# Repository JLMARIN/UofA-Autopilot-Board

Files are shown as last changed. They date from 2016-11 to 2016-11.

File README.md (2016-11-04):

# UofA-Autopilot-Board
University of Alberta Autopilot Board Hardware Design

This repository holds the design files for the University of Alberta Autopilot Board, currently being used by the University of Alberta Aerial Robotics Group (UAARG).

This project was developed by Jorge Marin, Rijesh Augustine and Duncan G. Elliott, from the University of Alberta ECE department.

The current design files include both the autopilot board and the redundant power supply board inside a single file. both board are connected by a breakaway tab. The reason for keeping both boards together is for reducing manufacturing costs. They can be separted afterwards.

A user guide is also included that contains comprehensive information about the autopilot board. A similar guide for the redundant power supply board is under work right now and will be available once finished.

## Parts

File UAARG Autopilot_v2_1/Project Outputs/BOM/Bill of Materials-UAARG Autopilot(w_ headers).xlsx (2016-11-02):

Designator | Description | Quantity | Value | Manufacturer | Manufacturer Part Number | Supplier 1 | Supplier Part Number 1
C1, C2 | Capacitor | 2 | 10pF | Yageo | CC0402JRNPO9BN100 | Digi-Key | 311-1014-1-ND
C3, C4, C5, C23, C36, C49, C67, C80 | Capacitor | 8 | 2.2uF | Yageo | CC0402MRX5R5BB225 | Digi-Key | 311-1442-1-ND
C6, C24 | Capacitor | 2 | 4.7uF | Yageo | CC0603KRX5R6BB475 | Digi-Key | 311-1455-1-ND
C7, C8, C9, C10, C12, C13, C15, C16, C19, C20, C22, C35, C48, C52, C53, C54, C55, C56, C66, C79, C83 |  | 21 | 100nF | Yageo | CC0402KRX7R6BB104 | Digi-Key | 311-1345-1-ND
C11 | Capacitor | 1 | 1uF | Yageo | CC0402KRX5R5BB105 | Digi-Key | 311-1438-1-ND
C14 | Capacitor | 1 | 2.2nF | Yageo | CC0402KRX7R9BB222 | Digi-Key | 311-1037-1-ND
C17, C38, C51, C69, C82 | Capacitor | 5 | 4.7uF | Yageo | CC0402MRX5R6BB475 | Digi-Key | 311-1734-1-ND
C18 | Capacitor | 1 | 220nF | Yageo | CC0402KRX5R5BB224 | Digi-Key | 311-1681-1-ND
C21 | Polarized Capacitor | 1 | 33uF | Kemet | T491A336K010AT | Digi-Key | 399-5279-1-ND
C25, C37, C50, C68, C81 | Capacitor | 5 | 10nF | Yageo | CC0402KRX7R7BB103 | Digi-Key | 311-1042-1-ND
C27, C40, C58, C71 | CAP CER 0.1UF 10V 10% X7R 0402 | 4 | 0.47uF | Yageo | CC0402ZRY5V7BB474 | Digi-Key | 311-1735-1-ND
C28, C41, C59, C72 | Capacitor | 4 | 10uF | Samsung Electro-Mechanics America, Inc. | CL32B106KBJNNNE | Digi-Key | 1276-3387-1-ND
C29, C42, C60, C73 | Capacitor | 4 | 4.7uF | Samsung Electro-Mechanics America, Inc. | CL32B475KBUYNNE | Digi-Key | 1276-1292-1-ND
C30, C43, C61, C74 | CAP CER 0.1UF 10V 10% X7R 0402 | 4 | 100pF | Yageo | CC0402JRNPO9BN101 | Digi-Key | 311-1024-1-ND
C31, C32, C44, C45, C62, C63, C75, C76 | Capacitor | 8 | 47uF | Murata Electronics North America | GRM32ER71A476KE15L | Digi-Key | 490-5312-1-ND
C33, C46, C64, C77 | Capacitor | 4 | 10uF | Yageo | CC0805KKX5R7BB106 | Digi-Key | 311-1865-1-ND
C34, C47, C65, C78 | Capacitor | 4 | 100nF | Yageo | CC0603KPX7R7BB104 | Digi-Key | 311-1335-1-ND
C85, C86 | Capacitor | 2 | 8.2pF | Yageo | CC0402BRNPO9BN8R2 | Digi-Key | 311-1628-1-ND
C87 | Polarized Capacitor | 1 | 11mF | Seiko Instruments | CPH3225A | Digi-Key | 728-1067-1-ND
C88 | Capacitor | 1 | 33nF | Samsung Electro-Mechanics America, Inc. | CL05B333JO5NNNC | Digi-Key | 1276-1553-1-ND
C89 | Capacitor | 1 | 470pF | TDK Corporation | C1005C0G1H471J050BA | Digi-Key | 445-2656-1-ND
D1, D2 | Typical Schottky Diode | 2 |  | Toshiba Semiconductor and Storage | CMS04(TE12L,Q,M) | Digi-Key | CMS04(TE12LQM)CT-ND
D3 | Typical SchottkyDiode | 1 |  | Diodes Incorporated | 1N5819HW-7-F | Digi-Key | 1N5819HW-FDICT-ND
D4 | Typical Diode | 1 |  | Micro Commercial Co | 1N4148WX-TP | Digi-Key | 1N4148WXTPMSCT-ND
EX1, EX2 | Header, 10-Pin | 2 |  | Sullins Connector Solutions | NPPN101BFCN-RC | Digi-Key | S5751-10-ND
J6, J11, J12, J13, J14, J20 | Header, 4-Pin | 6 |  | Molex, LLC | 0533980471 | Digi-Key | WM7608CT-ND
J16 | Header, 6-Pin | 1 |  | 3M | 961106-5500-AR-PR | Digi-Key | 3M9501CT-ND
J17 | U.FL RF connector | 1 |  | Hirose Electric Co Ltd | U.FL-R-SMT(10) | Digi-Key | H9161CT-ND
J18 | SMA RF connector | 1 |  | Cinch Connectivity Solutions Johnson | 142-0701-801 | Digi-Key | J502-ND
J19 | Header, 7-Pin | 1 |  | Molex, LLC | 0533980771 | Digi-Key | WM7611CT-ND
J21 | Header, 5-Pin | 1 |  | Molex, LLC | 0533980571 | Digi-Key | WM7609CT-ND
JTAG1 | Mini JTAG connector header 10 pos 5x2 pitch 1.27mm TH | 1 |  | Samtec Inc. | FTSH-105-01-F-DV-K | Digi-Key | SAM8796-ND
L1 | BEAD FERRITE | 1 |  | Murata Electronics North America | BLM15AX102SN1D | Digi-Key | 490-5442-1-ND
L2, L3, L4, L5 | FIXED IND 6.8UH 7A 33.4 MOHM SMD | 4 | 6.8uH | Vishay Dale | IHLP3232DZER6R8M11 | Digi-Key | 541-1355-1-ND
L6 | Chip Inductor | 1 | 6.8nH | Murata Electronics North America | LQW15AN6N8H00D | Digi-Key | 490-6841-1-ND
L7 | Chip Inductor | 1 | 27nH | Murata Electronics North America | LQW15AN27NJ00D | Digi-Key | 490-1151-1-ND
LED1, LED5 | LED RED CLEAR 0603 SMD | 2 |  | Lite-On Inc. | LTST-C190KRKT | Digi-Key | 160-1436-1-ND
LED2 | LED ORANGE CLEAR 0603 SMD | 1 |  | Lite-On Inc. | LTST-C190AKT | Digi-Key | 160-1180-1-ND
LED3, LED6, LED8, LED9 | LED GREEN CLEAR 0603 SMD | 4 |  | Lite-On Inc. | LTST-C190KGKT | Digi-Key | 160-1435-1-ND
LED4, LED7 | LED YELLOW CLEAR 0603 SMD | 2 |  | Lite-On Inc. | LTST-C190YKT | Digi-Key | 160-1184-1-ND
Q1 | NPN General Purpose Amplifier | 1 |  | Diodes Incorporated | MMDT5551-7-F | Digi-Key | MMDT5551-FDICT-ND
Q2 | N-CH MOSFET W/ DIODE DUAL PACKAGE | 1 |  | NXP Semiconductors | BSS138PS,115 | Digi-Key | 568-8393-1-ND
R1, R5, R9, R17, R26, R33, R40, R41, R46, R49, R56, R66, R67 | Resistor | 13 | 0 | Yageo | RC0402JR-070RL | Digi-Key | 311-0.0JRCT-ND
R2 | Resistor | 1 | 9.1K | Yageo | RC0603FR-079K1L | Digi-Key | 311-9.10KHRCT-ND
R3 | Resistor | 1 | 2.2K | Yageo | RC0603FR-072K2L | Digi-Key | 311-2.20KHRCT-ND
R6, R10 | Resistor | 2 | 1K | Yageo | RC0402FR-071KL | Digi-Key | 311-1.00KLRCT-ND
R7, R8, R11, R12, R15, R23, R42, R43, R44, R45, R65 | Resistor | 11 | 10K | Yageo | RC0402FR-0710KL | Digi-Key | 311-10.0KLRCT-ND
R13, R14 | Resistor | 2 | 2.2K | Yageo | RC0402FR-072K2L | Digi-Key | 311-2.20KLRCT-ND
R16 | Resistor | 1 | 120 | Yageo | RC0402FR-07120RL | Digi-Key | 311-120LRCT-ND
R18 | Resistor | 1 | 470 | Yageo | RC0402JR-07470RL | Digi-Key | 311-470JRCT-ND
R22, R27, R34, R50, R57 | Resistor | 5 | 100K | Yageo | RC0402FR-07100KL | Digi-Key | 311-100KLRCT-ND
R24, R31, R47, R54 | Resistor | 4 | 1Meg | Rohm Semiconductor | MCR01MRTF1004 | Digi-Key | RHM1.00MCDCT-ND
R25, R32, R48, R55 | Resistor | 4 | 453K | Yageo | RC0603FR-07453KL | Digi-Key | 311-453KHRCT-ND
R28, R35, R51, R58 | Resistor | 4 | 249K | Rohm Semiconductor | MCR01MRTF2493 | Digi-Key | RHM249KCDCT-ND
R30, R37, R53, R60 | Resistor | 4 | 100K | Yageo | RC0603FR-07100KL | Digi-Key | 311-100KHRCT-ND
R38, R39 | Resistor | 2 | 200K | Yageo | RC0402FR-07200KL | Digi-Key | 311-200KLRCT-ND
R61 | Resistor | 1 | 100 | Yageo | RC0402FR-07100RL | Digi-Key | 311-100LRCT-ND
R68 | Resistor | 1 | 10 | Yageo | RC0402FR-0710RL | Digi-Key | 311-10.0LRCT-ND
RN1, RN2, RN8, RN9 | Isolated Resistor Network | 4 | 1K | Yageo | YC164-JR-071KL | Digi-Key | YC164J-1.0KCT-ND
RN3 | Isolated Resistor Network | 1 | 10K | Yageo | YC164-JR-0710KL | Digi-Key | YC164J-10KCT-ND
RN4, RN5 | Isolated Resistor Network | 2 | 2.2K | Yageo | YC164-JR-072K2L | Digi-Key | YC164J-2.2KCT-ND
RN6, RN7 | Isolated Resistor Network | 2 | 470 | Yageo | YC164-JR-07470RL | Digi-Key | YC164J-470CT-ND
S1 | SWITCH TACTILE SPST-NO 0.05A 32V | 1 |  | C&K Components | KMR221GLFS | Digi-Key | 401-1427-1-ND
U1 | ARM Cortex-M4 32-bit MCU+FPU, 210 DMIPS, 1024 kB Flash, 192 kB Internal RAM, 51 I/Os, 64-pin LQFP, -40 to 85 degC, Tray | 1 |  | STMicroelectronics | STM32F405RGT6 | Digi-Key | 497-11767-ND
U2 | MS5611-01BA03 Barometer, Altimeter | 1 |  | Measurement Specialties, Inc. | MS5611-01BA03 | Digi-Key | 223-1622-1-ND
U3 | Invense MPU-6000 6 Axis Motion Sensor | 1 |  | InvenSense | MPU-6000 | Digi-Key | 1428-1005-2-ND
U4 | HMC5883L 3-axis Magnetometer | 1 |  | Honeywell Microelectronics & Precision Sensors | HMC5883L-TR | Digi-Key | 342-1082-1-ND
U5 | MAX3051 CAN Transceiver | 1 |  | Maxim Integrated | MAX3051EKA+T | Digi-Key | MAX3051EKA+TCT-ND
U6 | IC REG LDO 3.3V 1A SOT223 | 1 |  | Texas Instruments | LM3940IMPX-3.3/NOPB | Digi-Key | LM3940IMPX-3.3/NOPBCT-ND
U7 | LP2992 LDO Voltage Regulator | 1 |  | Texas Instruments | LP2992AIM5-3.3/NOPB | Digi-Key | LP2992AIM5-3.3/NOPBCT-ND
U8, U10, U19, U21 | Simple Switcher 3.5V to 36V 3A Synchronous Step-Down Voltage Converter | 4 |  | Texas Instruments | LM43603PWPT | Digi-Key | 296-37755-1-ND
U13, U14 | IC VOLT-LEVEL TRANSLATOR SM8 | 2 |  | Texas Instruments | PCA9306DCTR | Digi-Key | 296-18509-1-ND
U15, U16 | SN74LVC125APWR | 2 |  | Texas Instruments | SN74LVC125APWR | Digi-Key | 296-1222-1-ND
U17 | GCT MEM2051-00-195-00-A | 1 |  | GLOBAL CONNECTOR TECHNOLOGY | MEM2051-00-195-00-A | Newark | 05W3557
U18 | 8-bit AVR Microcontroller, 32KB Flash, 1KB EEPROM, 2KB SRAM, 32-pin TQFP, Industrial Grade (-40∞C to 85∞C) | 1 |  | Atmel | ATMEGA328P-AU | Digi-Key | ATMEGA328P-AU-ND
U23 | u-blox MAX-7Q GNSS Module | 1 |  | u-blox | MAX-7Q | u-blox | MAX-7Q
U24 | GPS SAW Filter | 1 |  | Murata Electronics North America | SF1186K-3 | Digi-Key | 583-1182-1-ND
U25 | MAX2659 Low Noise Amplifier | 1 |  | Maxim Integrated | MAX2659ELT+T | Digi-Key | MAX2659ELT+TCT-ND
USB1 | Micro USB Connector Type B | 1 |  | Molex, LLC | 0473460001 | Digi-Key | WM17141CT-ND
Y1 | Crystal Oscillator with ground points | 1 |  | Abracon LLC | ABM8G-12.000MHZ-4Y-T3 | Digi-Key | 535-10901-1-ND
Y2 | Resonator with built in capacitors | 1 |  | Murata Electronics North America | CSTCE16M0V53-R0 | Digi-Key | 490-1198-1-ND
Z1, Z2 | VARISTOR 0603 | 2 |  | Bourns Inc. | CG0603MLC-05LE | Digi-Key | CG0603MLC-05LECT-ND

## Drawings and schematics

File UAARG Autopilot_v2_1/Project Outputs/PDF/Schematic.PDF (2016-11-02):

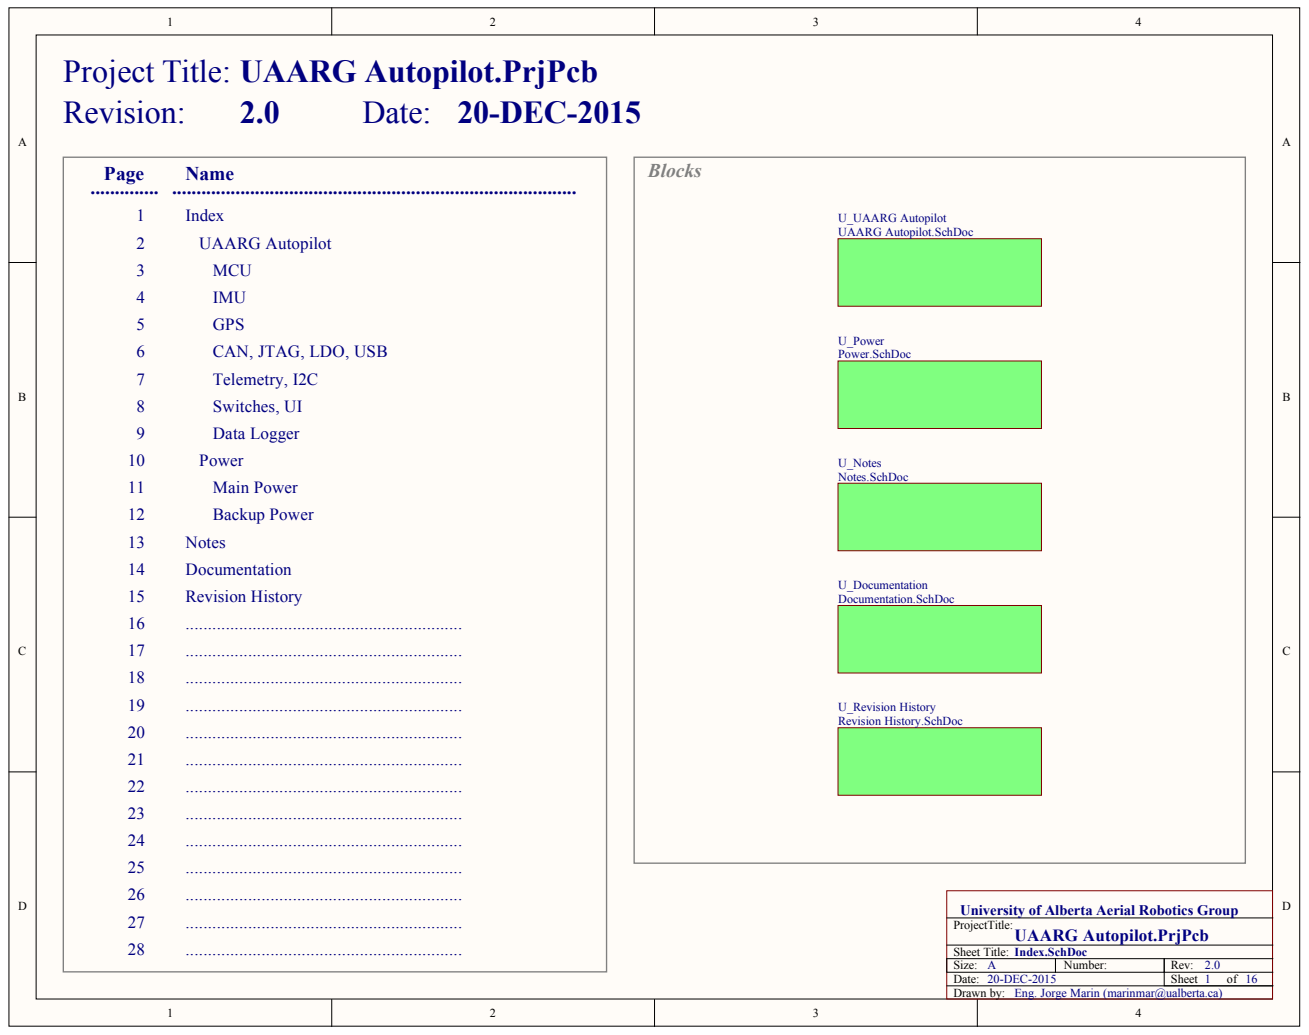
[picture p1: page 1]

University of Alberta Aerial Robotics Group
ProjectTitle:

Size: A | Number: | Rev:
Date: 20-DEC-2015 | | Sheet 1 of 16

Eng. Jorge Marin (marinmar@ualberta.ca)

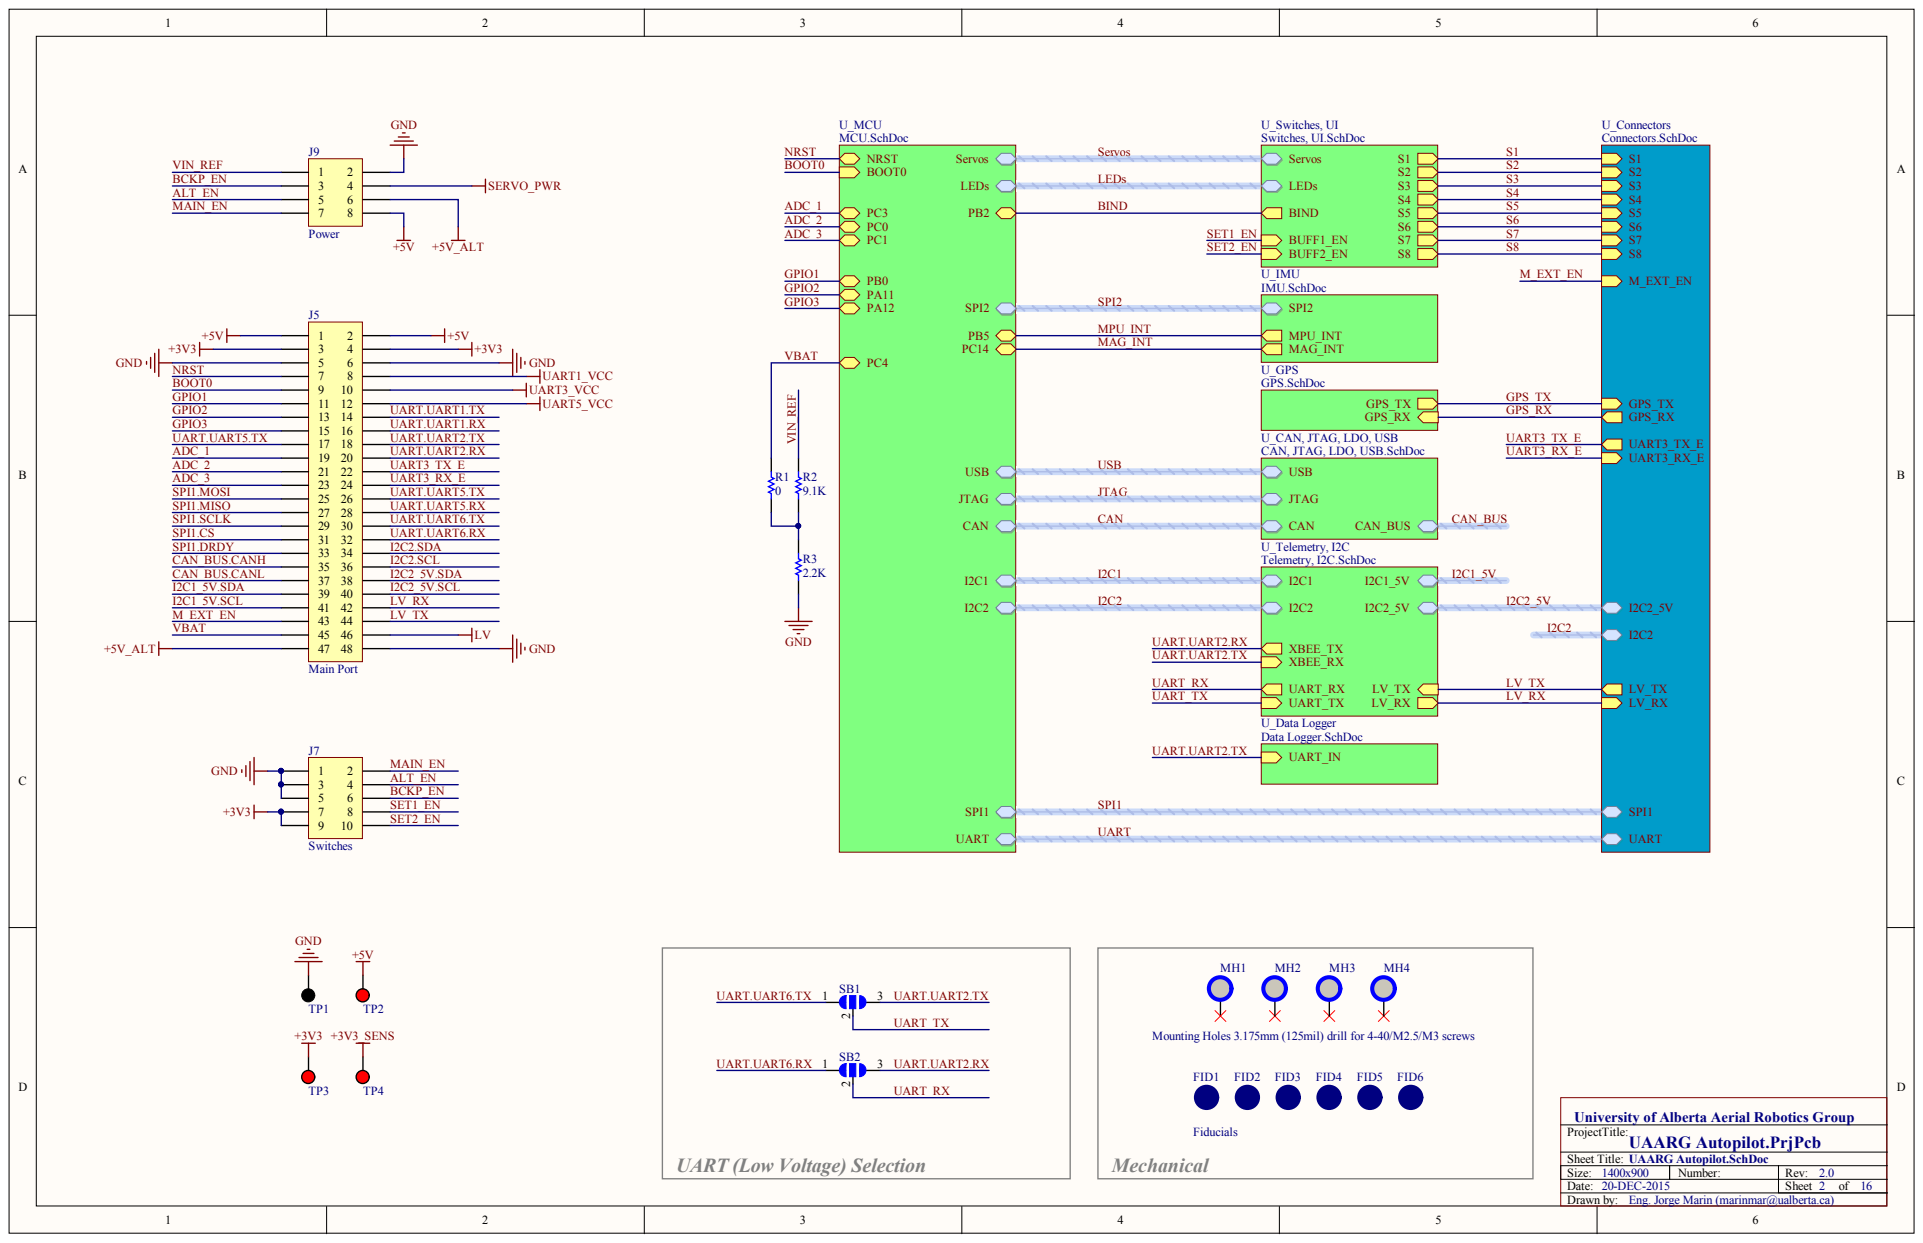
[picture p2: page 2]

U_CAN, JTAG, LDO, US
CAN, JTAG, LDO, USB.

Siz e : 1 4 0 0 x 9 0 0 | Numb er: | Re v : 2 . 0
Date : 2 0-DEC-2 0 1 5 | | S h e et 2 o f 1 6

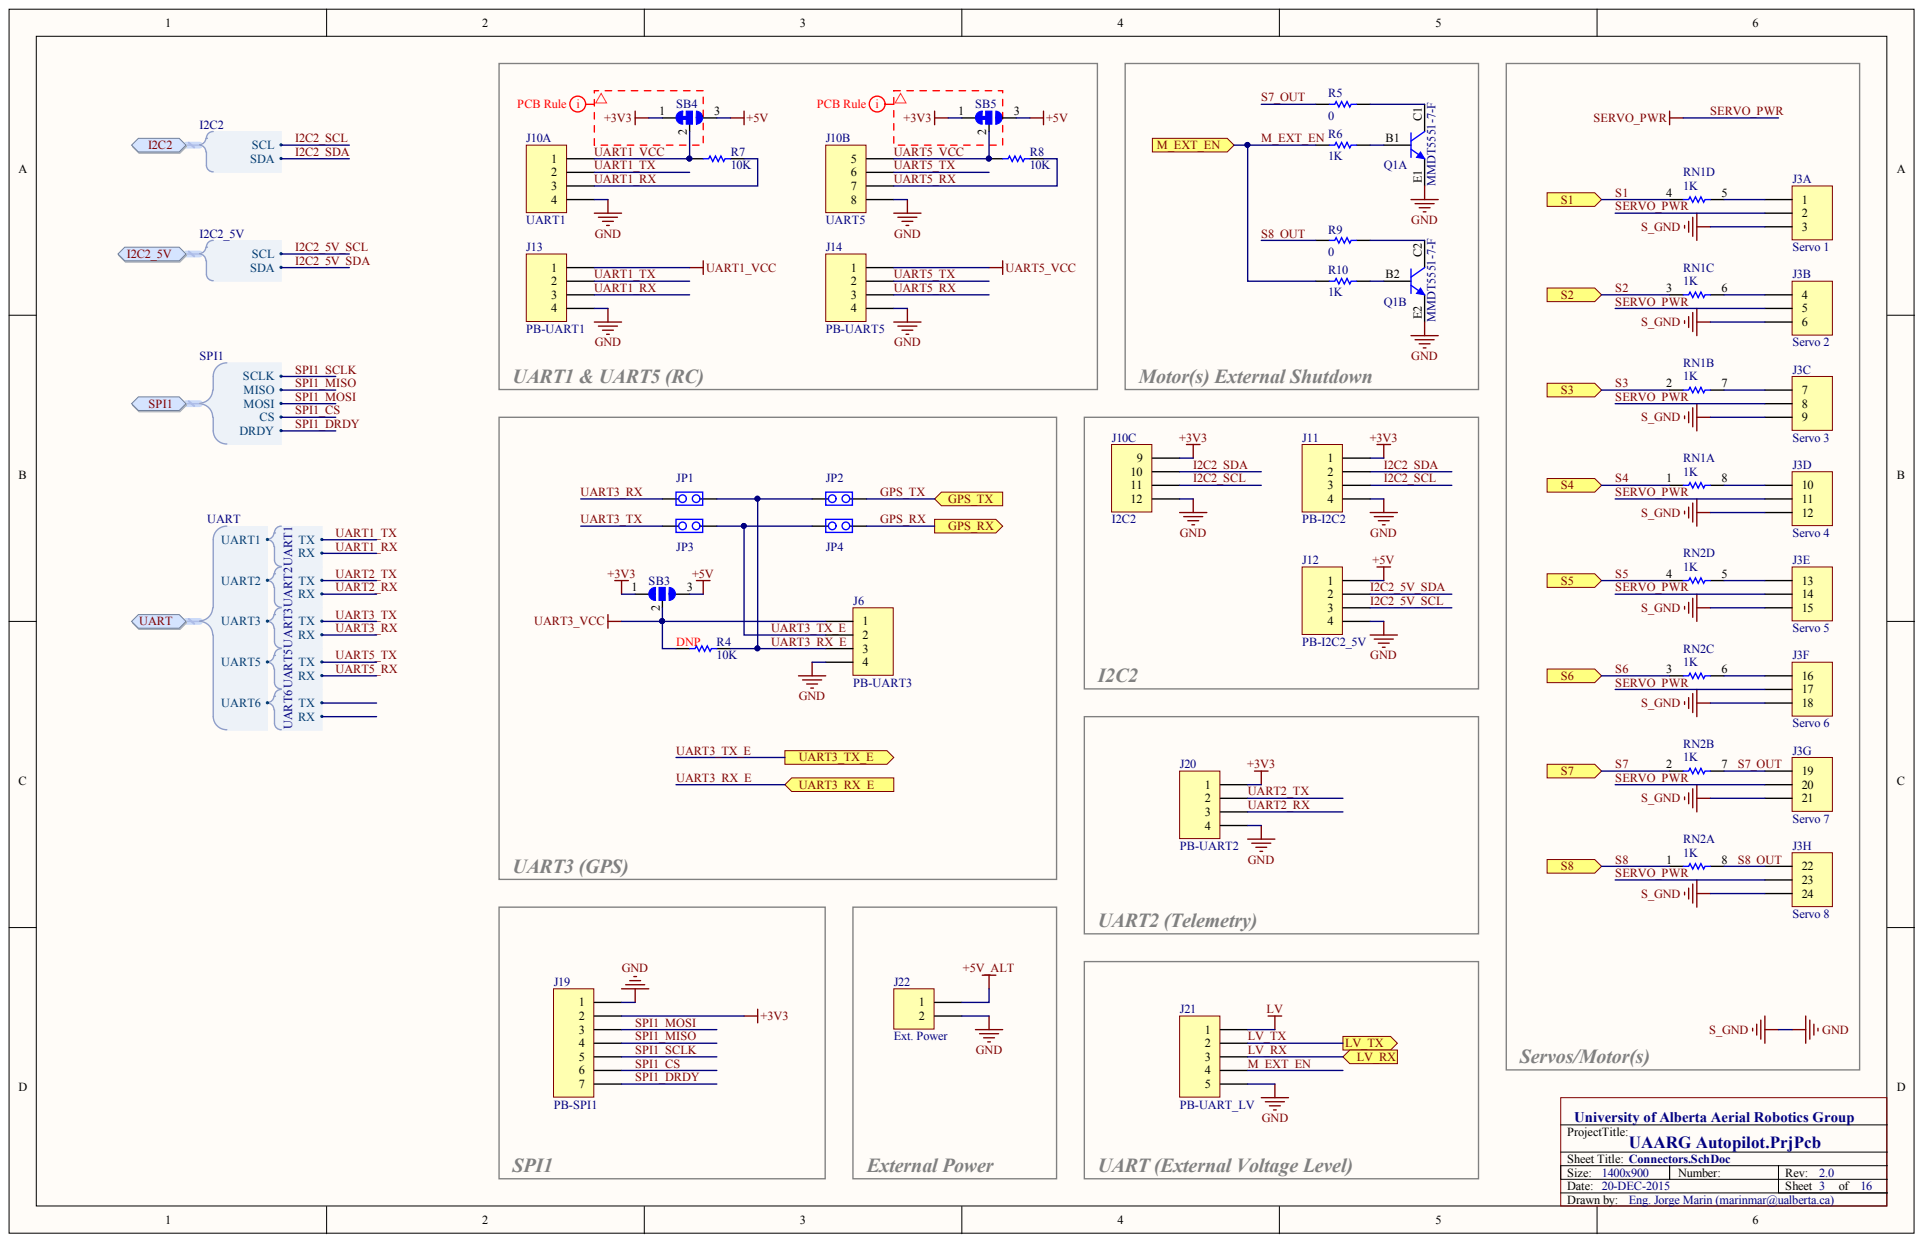
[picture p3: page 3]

University of Alberta Aerial Robotics Group
ProjectTitle:

UART (External Voltage Level)

Size: 1400x900 | Number: | Rev: 2.0
Date: 20-DEC-2015 | | Sheet 3 of 16

Eng. Jorge Marin (marinmar@ualberta.ca)

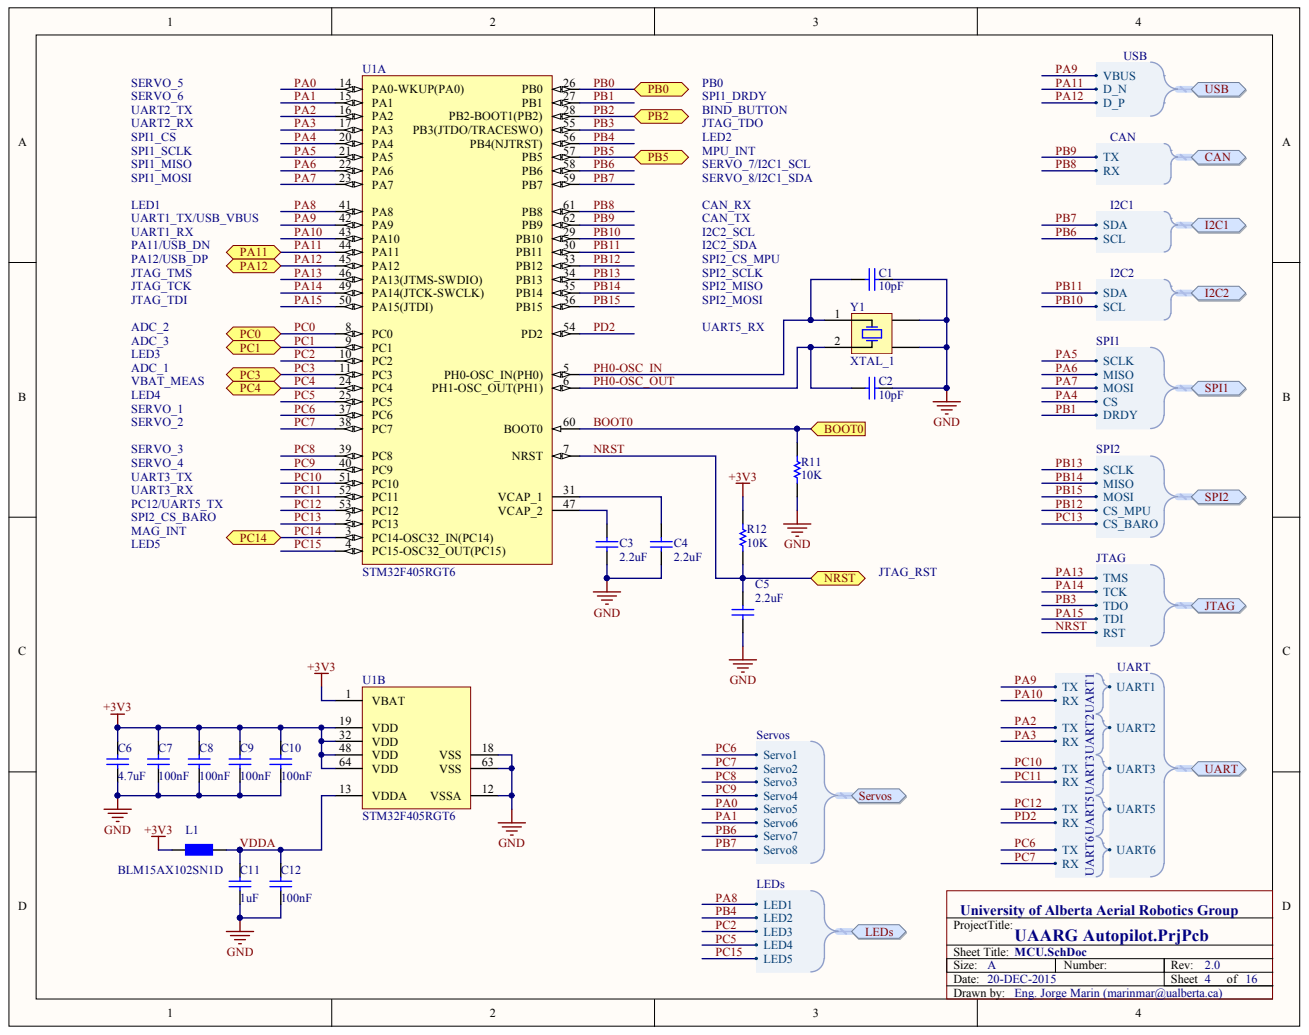
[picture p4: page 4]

S i z e : | Number: | Rev: 2.
D a t e : 20-D EC-2015 | | She e t 4 of 16

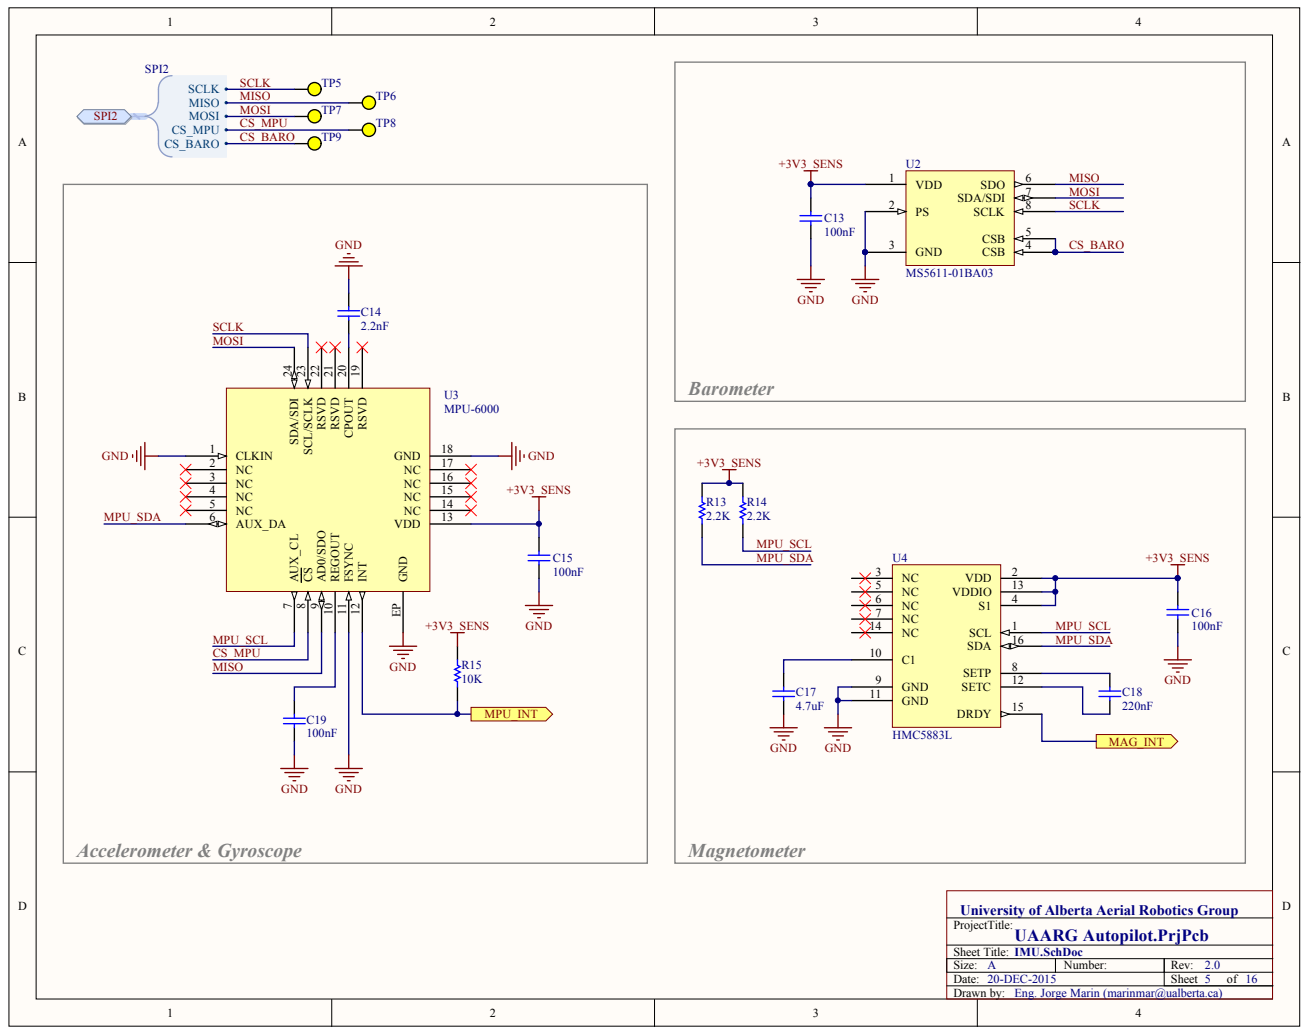
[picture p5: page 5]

4 | CS_BARO

S i z e : | Number: | Rev: 2.
D a t e : 20-D EC-2015 | | She e t 5 of 16

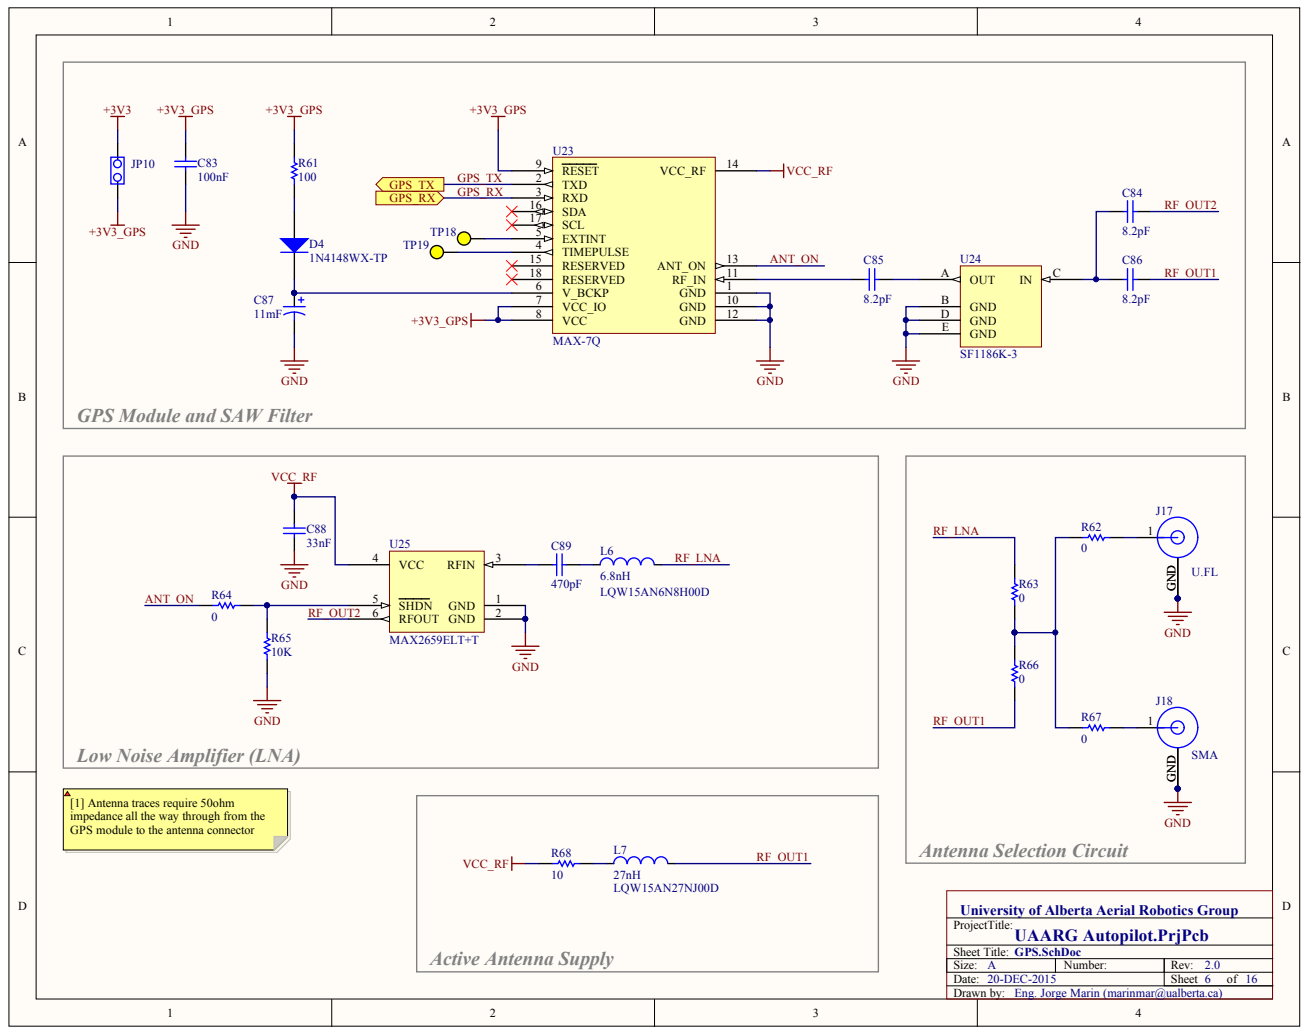
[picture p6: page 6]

GPS Module and SAW Filter

Low Noise Amplifier (LNA)

[1] Antenna traces require 50ohm
impedance all the way through from the
GPS module to the antenna connector

University of Alberta Aerial Robotics Group
ProjectTitle:

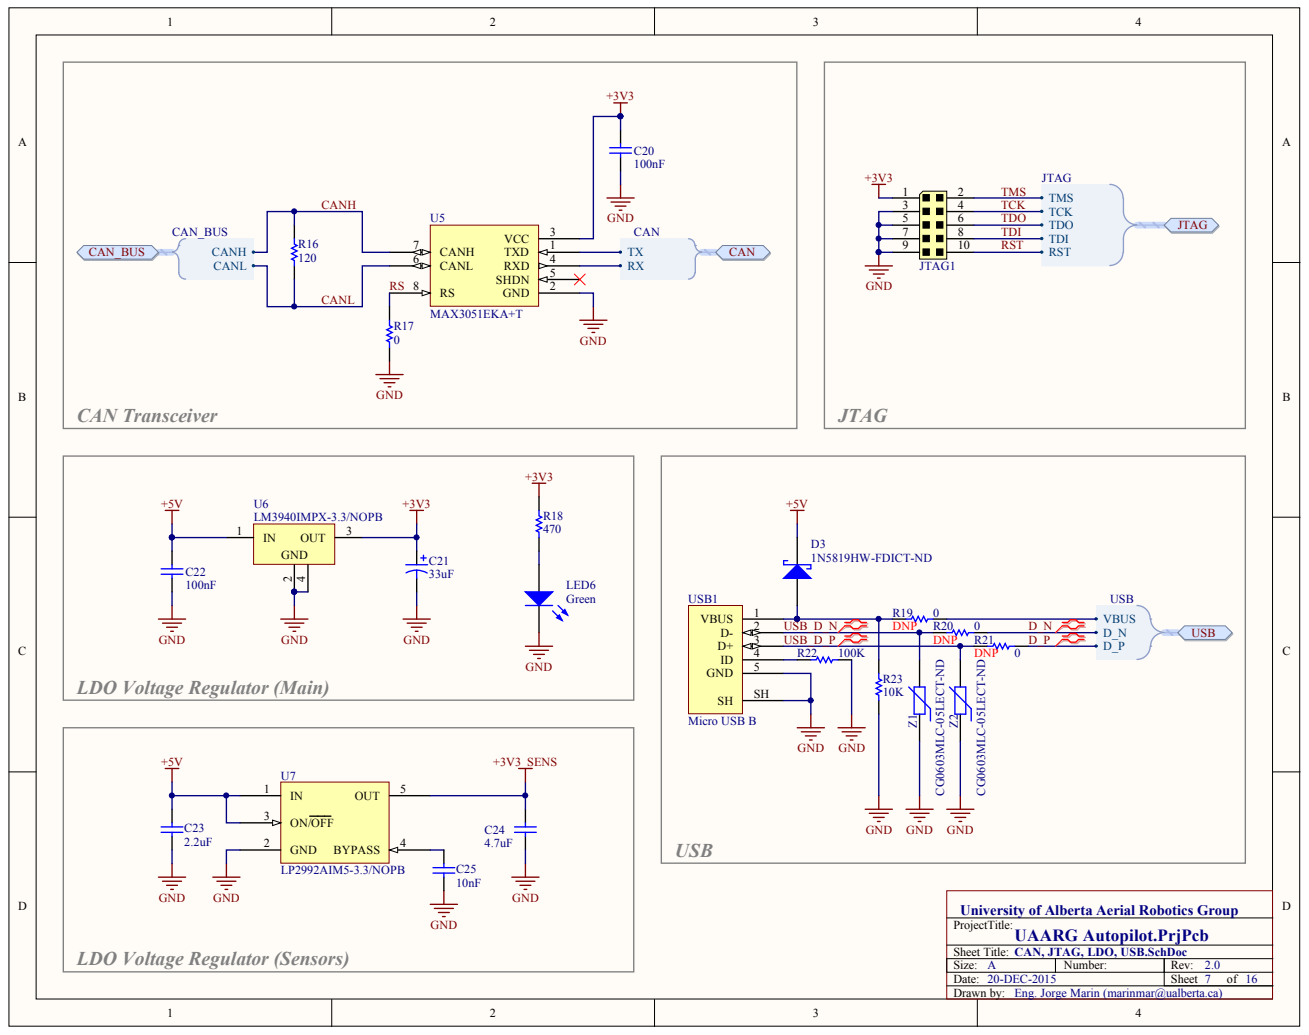
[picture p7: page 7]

LDO Voltage Regulator (Main)

University of Alberta Aerial Robotics Group
ProjectTitle:

UAARG Autopilot.PrjPcb
CAN, JTAG, LDO, USB.SchDoc

LDO Voltage Regulator (Sensors)

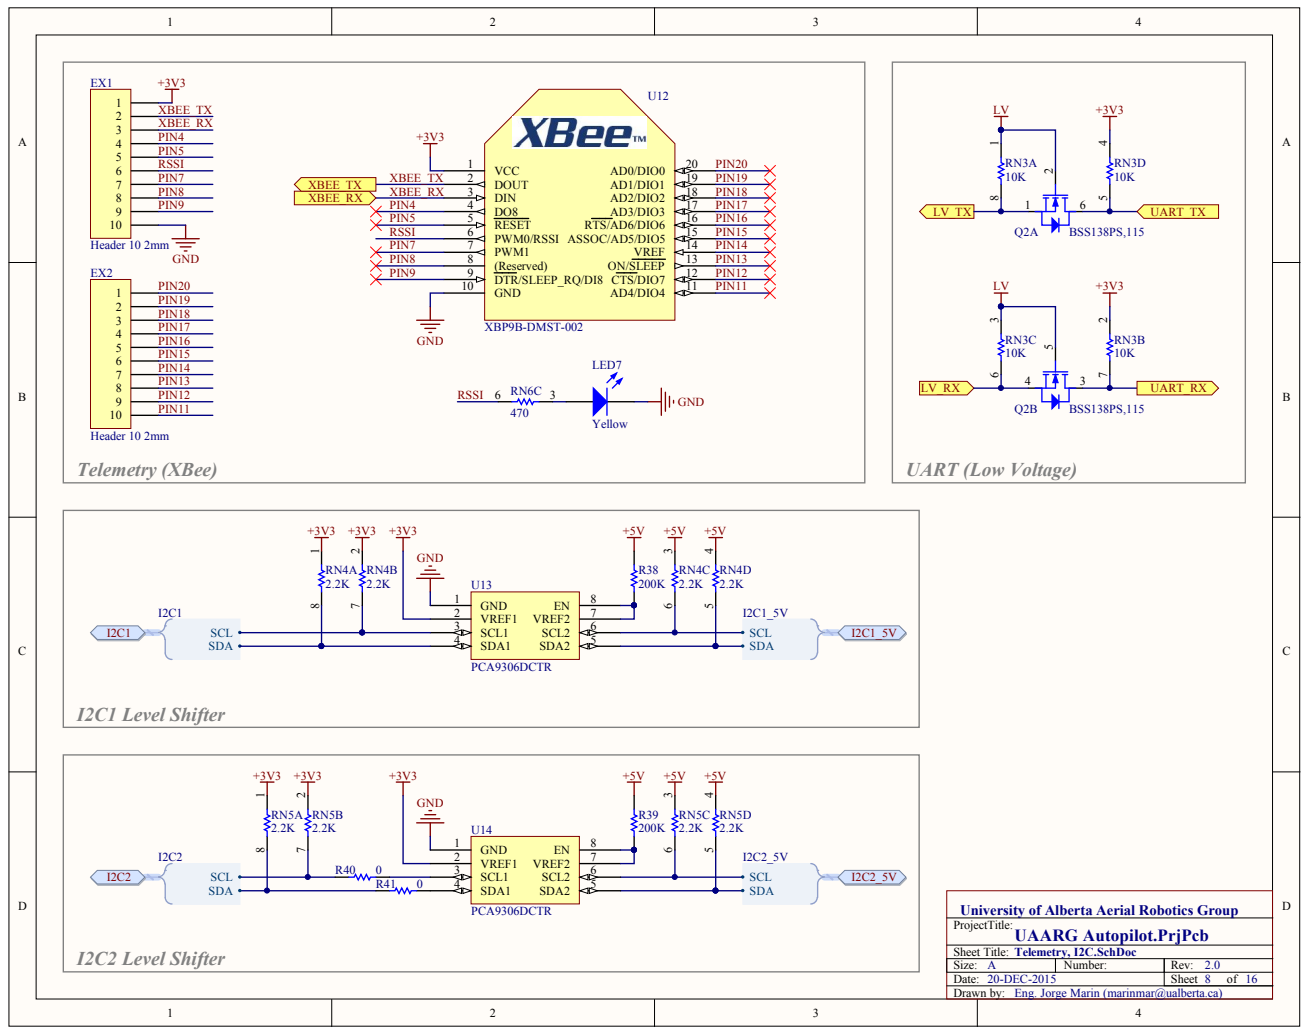
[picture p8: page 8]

University of Alberta Aerial Robotics Group
ProjectTitle:

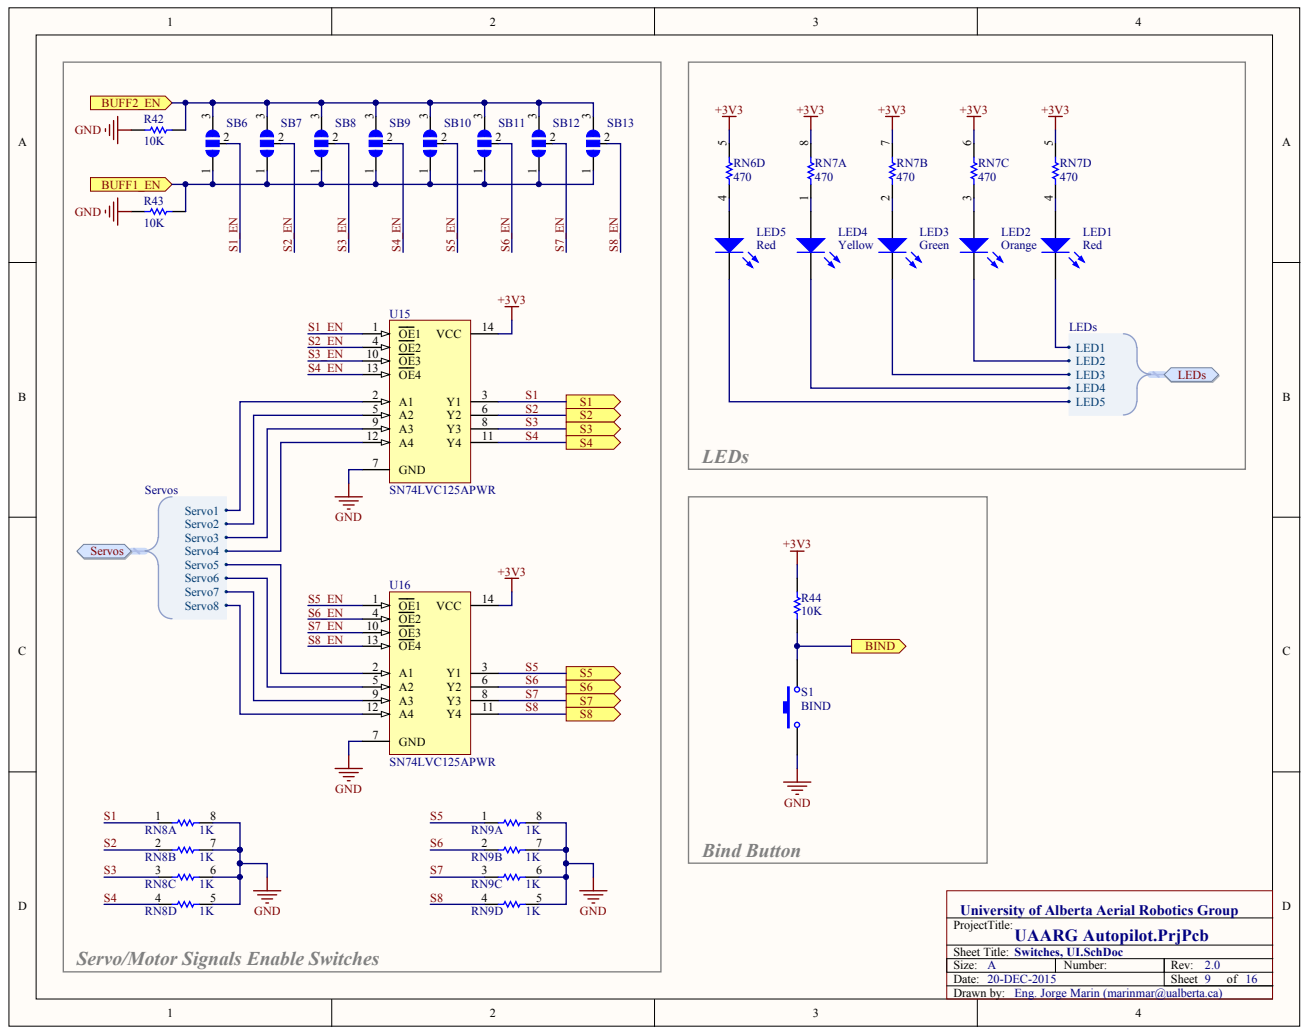
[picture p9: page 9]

University of Alberta Aerial Robotics Group
ProjectTitle:

Servo/Motor Signals Enable Switches

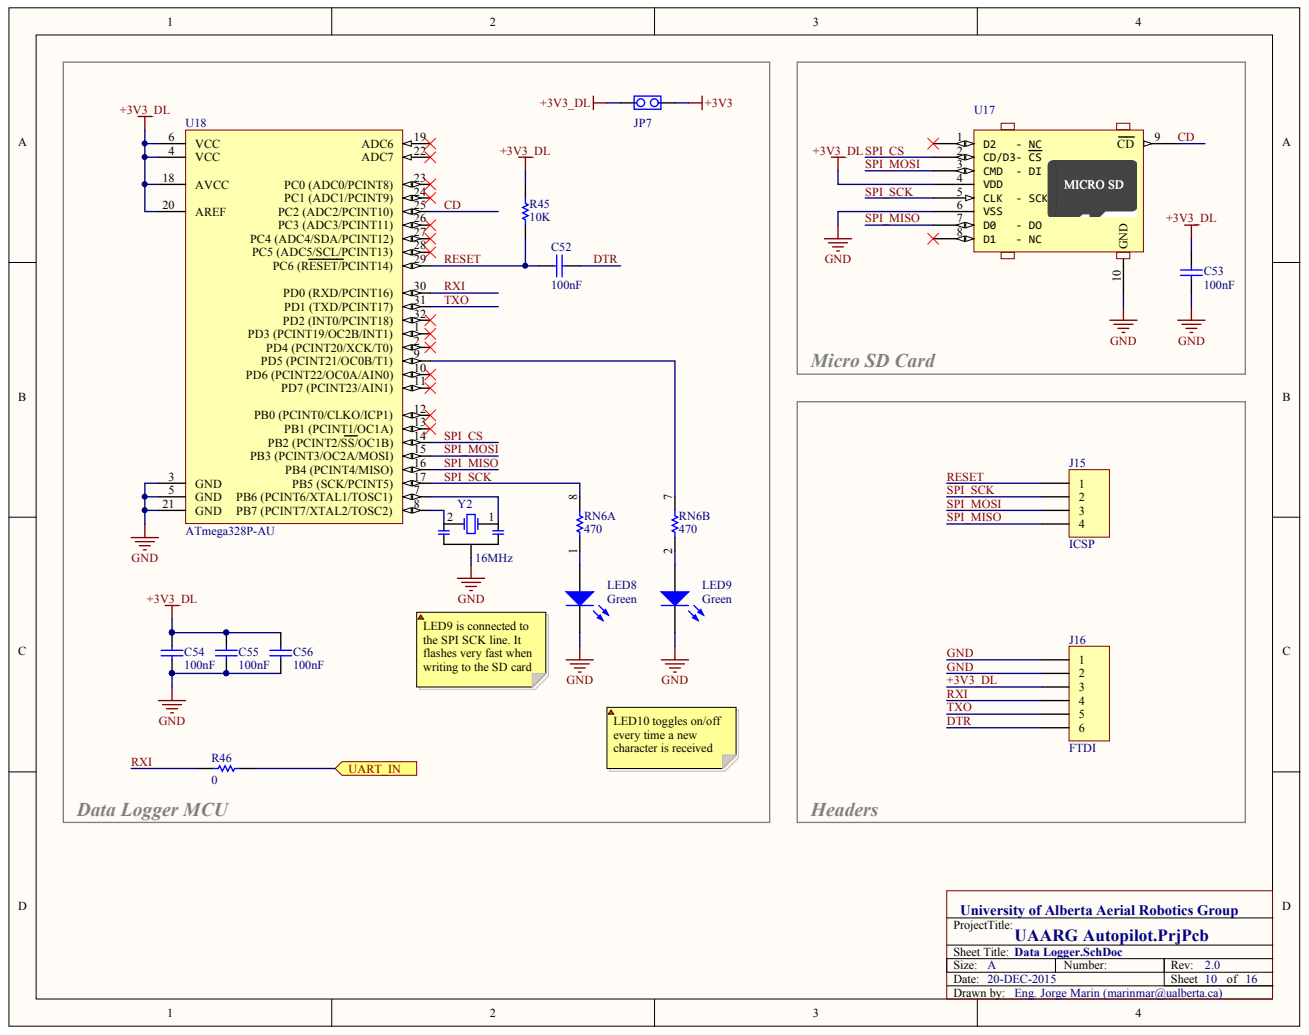
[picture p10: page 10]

University of Alberta Aerial Robotics Group
Proj

S i z e : | Number: | Rev: 2.
D a t e : 20-D | | She e t of

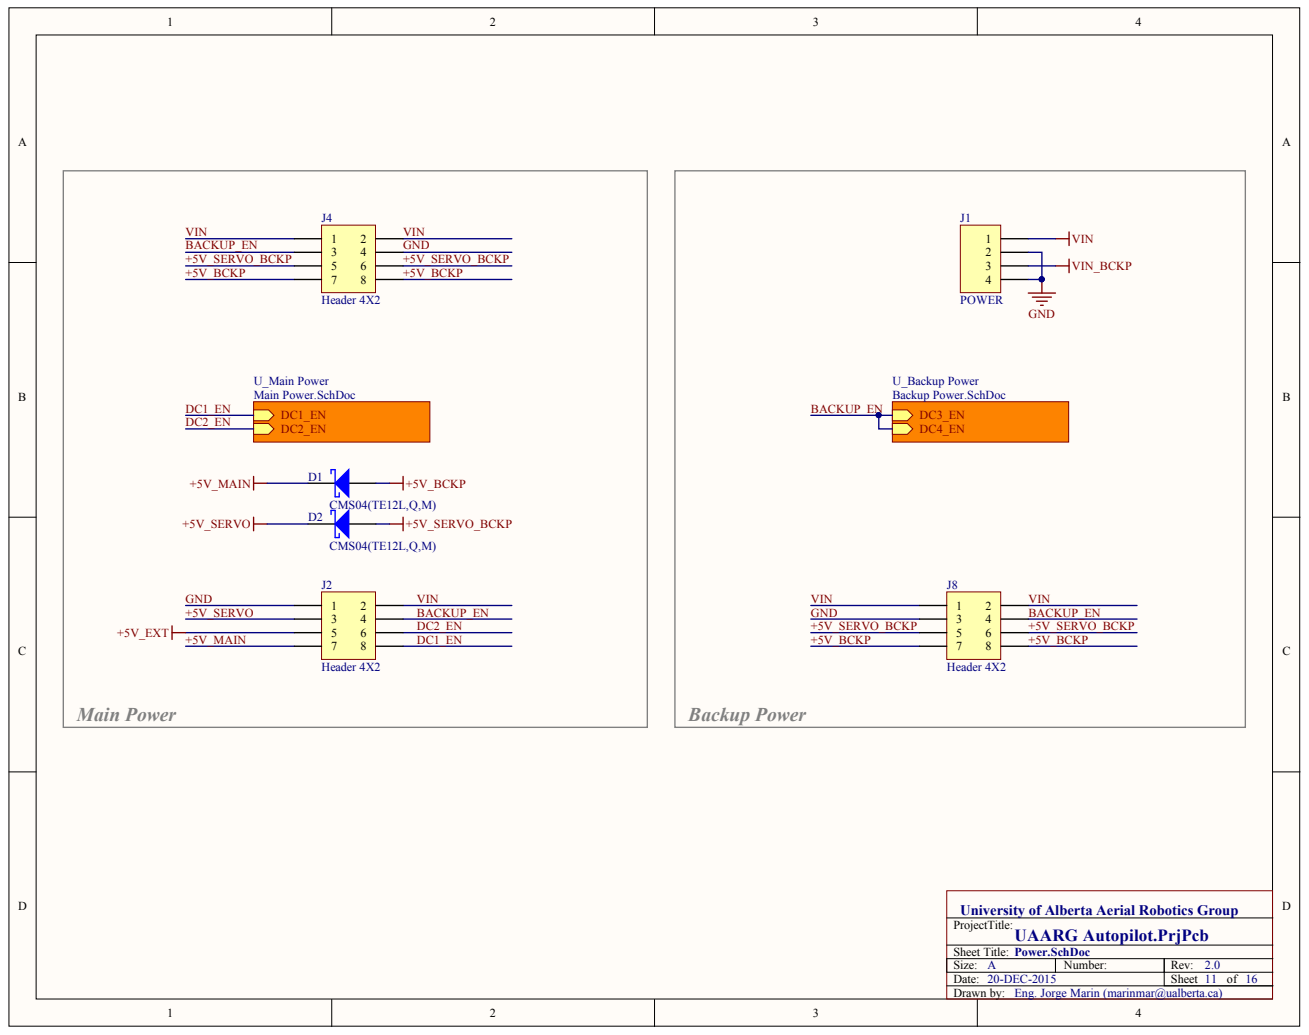
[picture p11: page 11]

University of Alberta Aerial Robotics Group
ProjectTitle:

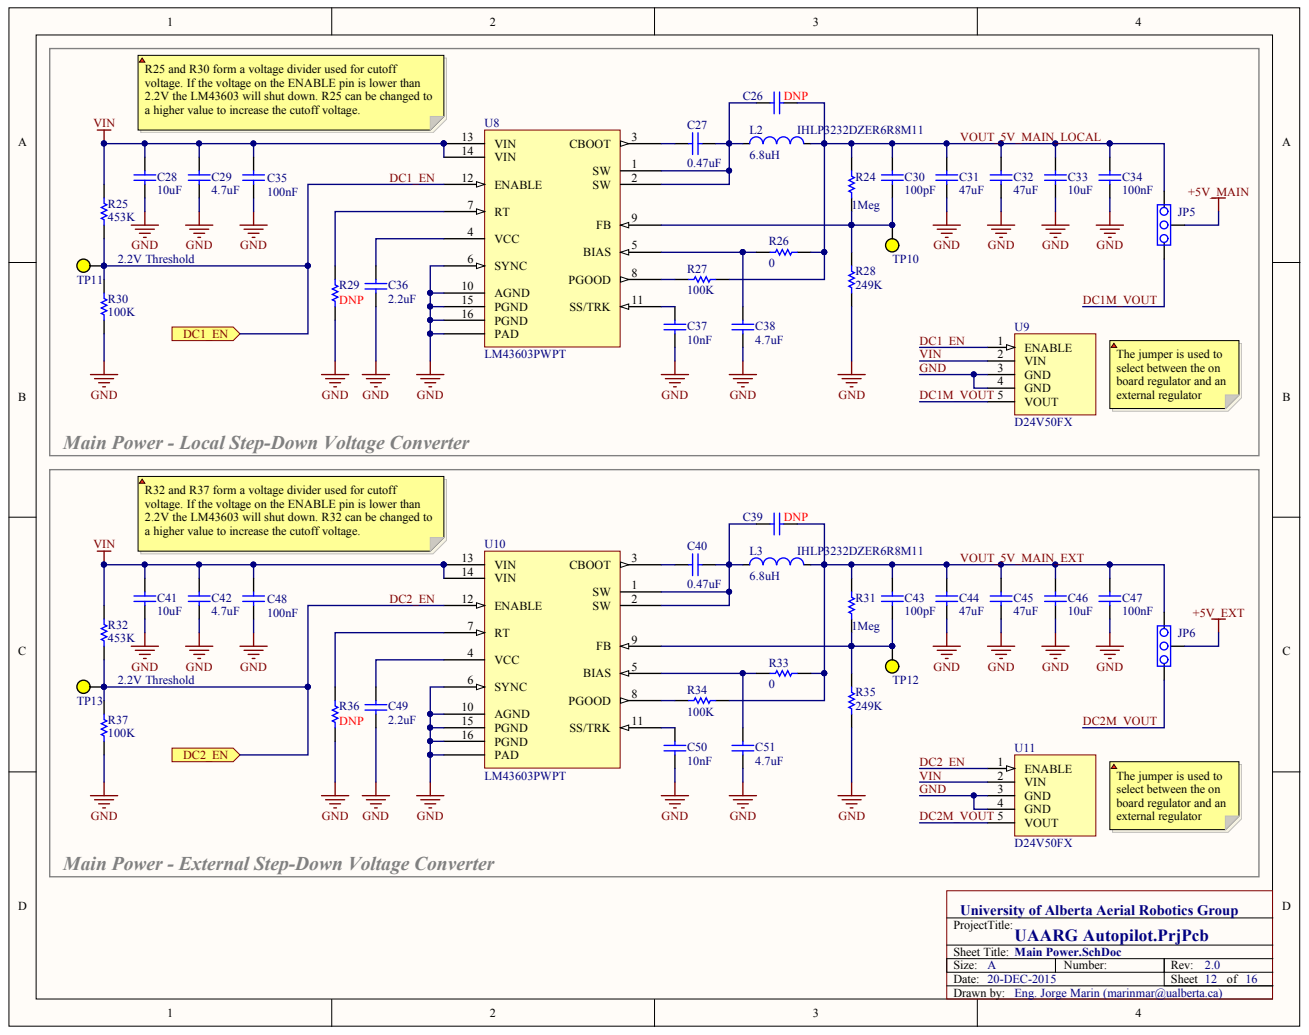
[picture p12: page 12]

R25 and R30 form a voltage divider used for cutoff
voltage. If the voltage on the ENABLE pin is lower than
2.2V the LM43603 will shut down. R25 can be changed to
a higher value to increase the cutoff voltage.

VCC 4

SYNC 6 AGND 10

PGND 15

The jumper is used to
select between the on
board regulator and an
external regulator

Main Power - Local Step-Down Voltage Converter

R32 and R37 form a voltage divider used for cutoff
2.2V the LM43603 will shut down. R32 can be changed to

Main Power - External Step-Down Voltage Converter

University of Alberta Aerial Robotics Group
ProjectTitle:


R48 and R53 form a voltage divider used for cutoff
voltage. If the voltage on the ENABLE pin is lower than
2.2V the LM43603 will shut down. R48 can be changed to
a higher value to increase the cutoff voltage.

VCC 4

SYNC 6 AGND 10

PGND 15

The jumper is used to
select between the on
board regulator and an
external regulator

Backup Power - Local Step-Down Voltage Converter

R55 and R60 form a voltage divider used for cutoff
2.2V the LM43603 will shut down. R55 can be changed to

Backup Power - Backup Servo Step-Down Voltage Converter

University of Alberta Aerial Robotics Group
ProjectTitle:


General notes relating to the design.

Layout notes referring to specific components or group of
components are indicated on the schematics by the note
number, enclosed in braces, adjacent to the component. Eg [1].

[1] GPS antenna traces require 50ohm

List of assembly variations. Variants are designated with a letter
starting from A. The description shows the Variant name in
brackets and then any comments.

Variant | Description

A B C | [w/o headers] All SMT components soldered. Through-hole headers are not included. [w/ headers] All SMT components soldered, including through-hole headers. [Assembled] All components are soldered and external components are plugged. Fully assembled board.

Copyright section (if applicable)

20-DEC-2015 | 14 16


SPI SLAVES AND "CHIP SELECT" PIN MAPPING

NAME | PERIPHERAL | MCU CS PIN

SPI2 | MPU-6000 | PB12

NAME | FUNCTION | MCU PIN | DEFAULT SET

UART1 | TX | PA9 | -

RX | PA10 | RC Receiver 1 TX

UART2 | TX | PA2 | XBee RX

RX | PA3 | XBee TX

UART3 | TX | PC10 | GPS RX

RX | PC11 | GPS TX

UART4 | TX | PA0 | SERVO_5

RX | PA1 | SERVO_6

UART5 | TX | PC12 | GPIO PC12

RX | PD2 | RC Receiver 2 TX

UART6 | TX | PC6 | SERVO_1

RX | PC7 | SERVO_2
